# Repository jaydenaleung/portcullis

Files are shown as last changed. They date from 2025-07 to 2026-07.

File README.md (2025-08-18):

# Portcullis - the boltlock unlocker

A portcullis originally guarded a castle's entrance, known for its waffle-like iron gates coming down to cover the entrance of the castle's archway following the moat bridge.
-

Portcullis is an automated system that mechanically unlocks home security door reinforcement locks (HSDRLs), with access protected by a passcode using a keypad. HSDRLs act as boltlocks when mounted onto the doorframe next to the door being locked. See below for more information.

VIDEO DEMO: [https://youtu.be/WndzgAl9owI](url)






*The large block in the picture represents the wall that HSDRLs are mounted onto.*



*A medival portcullis. Credit: [https://www.dreamstime.com/stock-images-castle-portcullis-image7831724](url).*

# Figures

**Total Minimum Cost:** $43 USD

**Total Hours Spent:** 92 hrs

**Total Days Spent:** 16 days

*See JOURNAL.md and the BOM below for an in-depth explanation of these numbers.*

# How It Works

How do HSDRLs work?
-

HSDRLs lock a door by acting as a fixed stopper. In combination with this, their tough metal material allows it to be one of the strongest, safest, and most secure locks on the market. After turning them to their locked position, they will 'click' into place, effectively fixing itself against the door. Mechanically, this means that when the door pushes against it, its rigid position will hold the door back. See the picture below for how unlocking and locking an HSDRL works.



Portcullis
-

This specific mechanism works to solve this issue in three steps: one, using a linear actuator to push the HSDRL forward enough that it can be rotated. Two, rotate it to unlock or lock the door. Three, retract the linear actuator to lock the HSDRL in place. This is all controlled by an Arduino Uno R3 microcontroller, which connects to a continuous servo powering the linear actuator and a positional servo rotating the mechanism. Additionally, the locking/unlocking process is initiated by either entering the correct passcode on a keypad on the side of the door opposite the lock or by pressing a button (passcode not required) on the same side of the door as the lock.



Additional Features
-

- 16x2 LCD interface to display entered PIN from the keypad
- Privacy covers when entering PIN - numbers show up as '*' instead of the entered number
- Three different possible screens for the LCD display
- Aesthetic microcontroller housing with LED lights on button
- Linear guide rails and tension springs for the linear actuator

Wiring Diagram
-

This project does not utilize a PCB because of the sparse placement of the connected parts. See this wiring diagram instead:



And this schematic:



# The 'Why' Behind the Project

This project actually started a while ago when I wanted to ensure that no one would could come into my room without my permission, as I felt back then that it had become an issue. Using my engineering skills to solve real-world issues, I initially worked on developing my own boltlock before realizing that it would be much more efficient to just purchase a boltlock. Unfortunately, I would occasionally get locked out of my room, which was a significant issue. I again began to solve this issue by taking an engineering approach to it and working a system that could lock and unlock the boltlock for me when I was outside of my room. In addition to having a keypad, I envision pairing this mechanism with my phone so that it will be more easily accessible, especially if something happens to break or the wires to the keypad snap.

# Why This Is Worth Six Points

With the three-part unlocking/locking system mentioned earlier, this is a mechanically complex project that requires precise control of the motors in order to ensure reliability and stability. I spent many hours designing a system for this (over half of my hours spent were in CAD and research), learning a lot about linear guide rails, springs, and their standardizations, and how to effectively approach a real-life issue using engineering. Additionally, I spent a significant amount of time and effort designing logic for the keypad, LCD screens, and LED button as well as making them all work smoothly in tandem. My effort spent doing this project, seen in the thirty hours of work done in addition to prior work and excluding the process of physically building the device, qualifies this project for six points.

# Bill of Materials (BOM):

*Note: I am using Aliexpress for some and Amazon for others. Prices listed below are in USD and per part. e.g. 2x Nema 17 ($14) = $28 total. Also see the .csv file for the official BOM.*

| Quantity | Name | Price Per Part | Link | Notes |
|---|---|---|---|---|
| 2 | MGN7C linear guide rail + carriage | $12.78 | https://www.aliexpress.us/item/3256804722090559.html | 150mm length |
| 4 | M2 50pcs bolt | $1.27 | https://www.aliexpress.us/item/2255799955713291.html | 4mm, 6mm, 8mm, 10mm lengths |
| 1 | M2 50pcs nut | $1.52 | https://www.aliexpress.us/item/3256807407546447.html |  |
| 1 | M3 30pcs bolt | $1.43 | https://www.aliexpress.us/item/2255799955713291.html | 6mm length |
| 1 | M3 50pcs nut | $1.68 | https://www.aliexpress.us/item/3256807407546447.html |  |
| 1 | 10 pcs Tension spring w/ hook | $4.09 | http://www.aliexpress.us/item/3256805190632211.html | 50mm length, 0.3mm wire diameter, 5mm outer diameter |
| 2 | Pushbutton | $3.06 | https://www.aliexpress.us/item/3256807837994773.html | Red color (NOT with the power symbol), 3-6V, 19mm size, momentary type |
| 1 | 3m length wire cover | $5.39 | https://www.aliexpress.us/item/3256808858896776.html | A-White (A-type, white and red color) |
| 1 | Heat gun + Heat shrink tubes | $9.99 | https://www.aliexpress.us/item/3256807579039319.html | 1060 pcs, 110V US plug |
| 1 | Keypad | N/A | https://a.co/d/2Og2Gza | Already have this (no price). |
| 1 | LCD | $2.39 | https://www.aliexpress.us/item/3256806852105736.html | I2C LCD Green |
| 1 | Power bank + USB-B cable | N/A | Any works | Already have this (no price). |
| 1 | Positional SG90 Servo | N/A | https://a.co/d/dwwxeeT | Already have this (no price). |
| 1 | Continuous FS90R Servo | N/A | https://a.co/d/2raoKgm | Already have this (no price). |
| 1 | Jumper wires | N/A | https://a.co/d/hYEySLh | Already have this (no price). |
| 1 | 1kg spool of filament | N/A | Any works | Any color, any type. Already have this (no price). |
| 1 | Home security door reinforcement lock | N/A | https://a.co/d/iCTK5DP | Already have this (no price). |
| 1 | 330Ω resistor | N/A | N/A | Already have this (no price). |

| **Total minimum cost** | $43.41 |
| --- | ---- |
| **Total including shipping; sales tax (assumed ~6%); import and customs fees; etc.** | ~$75 |

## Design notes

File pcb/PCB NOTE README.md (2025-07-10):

There is no required PCB for this project because of the unique positioning of the electronic components. Since the components are on different sides of the doors and the parts are not positioned so that they can be mounted onto the PCB anyways, a PCB is not necessary. The PCB was included for your reference and also because I did not realize this until I had made the whole PCB.

The wiring diagram can, alternatively, be found here: [https://app.cirkitdesigner.com/project/c432579e-b21c-4e14-8d9b-45fb584a04a3](https://app.cirkitdesigner.com/project/c432579e-b21c-4e14-8d9b-45fb584a04a3).

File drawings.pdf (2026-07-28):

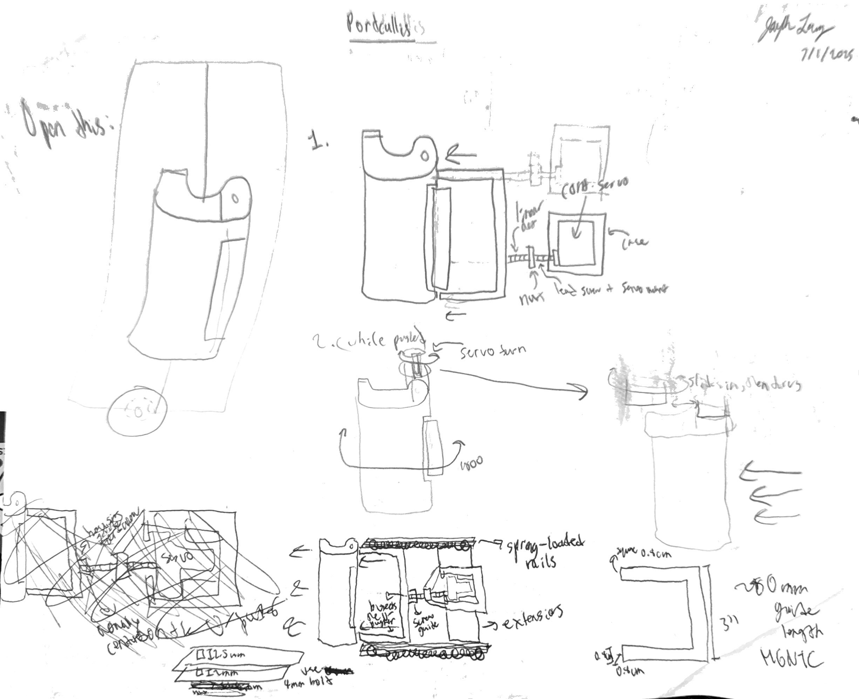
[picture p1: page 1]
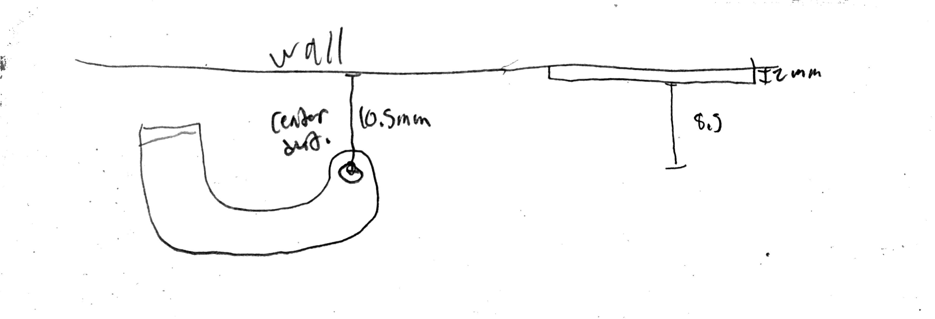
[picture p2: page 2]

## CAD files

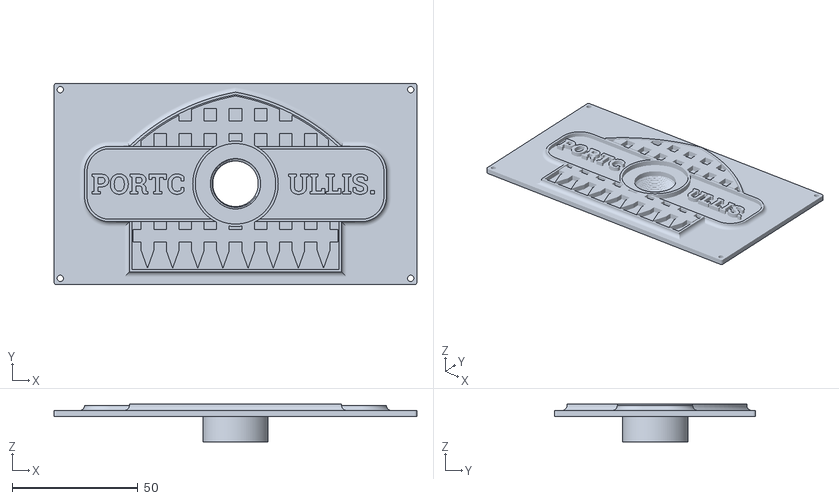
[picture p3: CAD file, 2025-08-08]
cad/parts to print/Arduino housing.stl
144.3 x 80.0 x 15.0

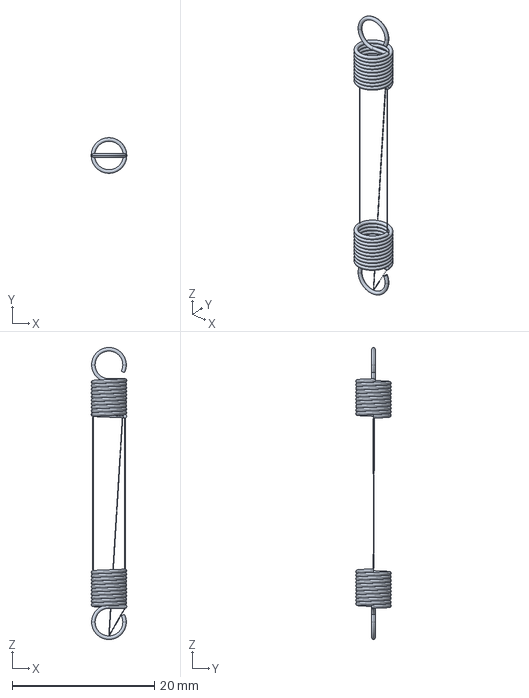
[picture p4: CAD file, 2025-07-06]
cad/reference parts/0.3mmWireD_5mmOutsideD_40mm_TorsionHookSpring/spring_t_050_050_0400_i_0.stp
5.00 x 5.00 x 41.0 mm

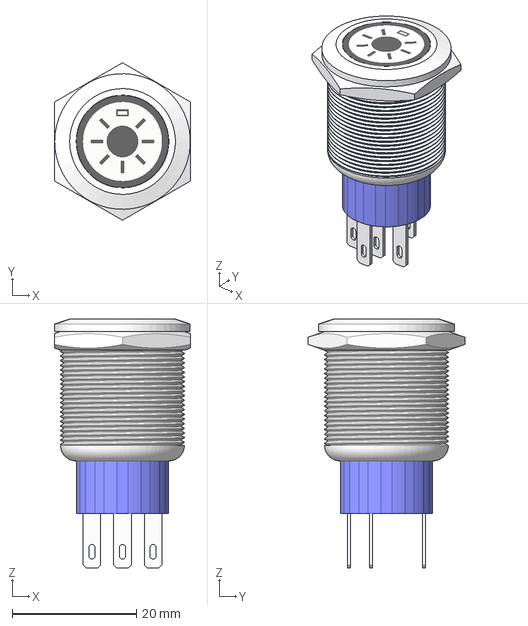
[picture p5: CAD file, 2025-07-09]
cad/reference parts/19mm_Momentary_OnOffButton/1_Push_Button v4.step
21.9 x 25.3 x 40.0 mm

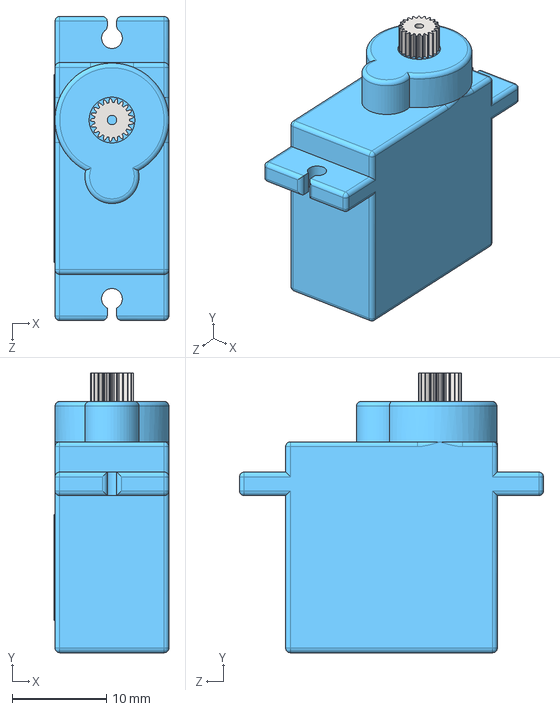
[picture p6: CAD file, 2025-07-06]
cad/reference parts/FITEC_FS90R_ContinuousServo/Fitec FS90R Micro Servo NoWires.STEP
12.2 x 29.7 x 32.3 mm

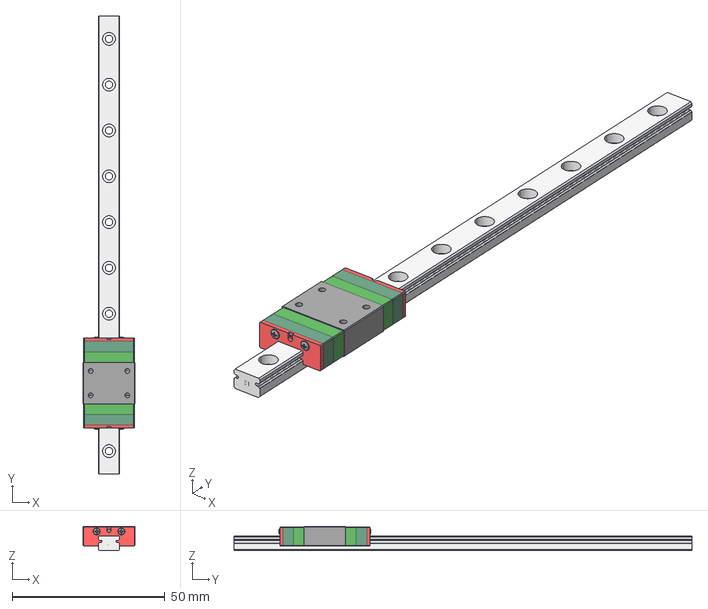
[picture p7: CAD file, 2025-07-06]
cad/reference parts/HIWIN_MGN7C_150mm_LinearGuideRail/MGN07C1R150ZFHM_EL_FILE_1.stp
17.0 x 150.0 x 8.00 mm

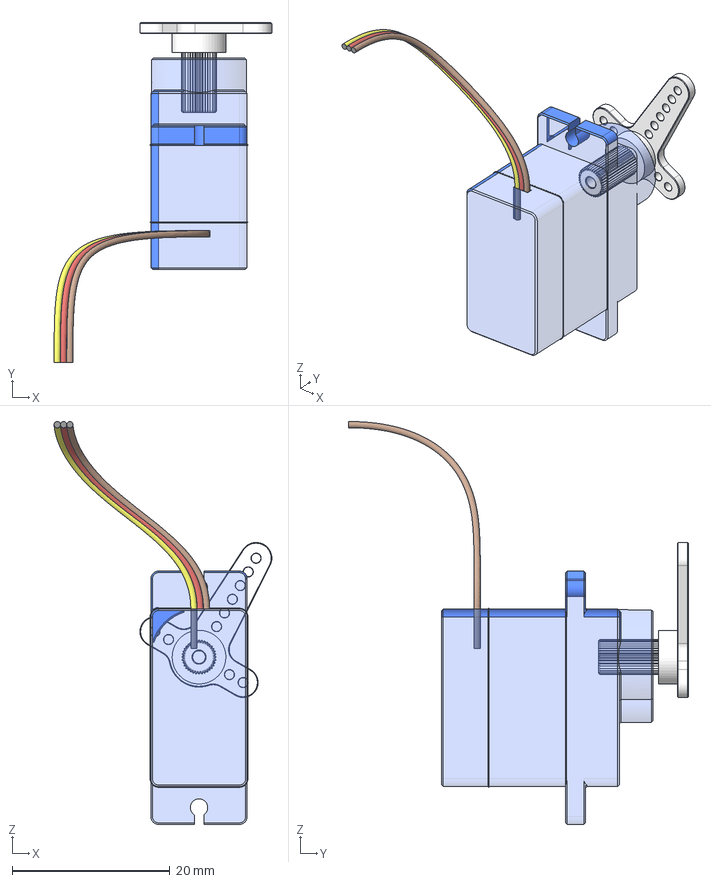
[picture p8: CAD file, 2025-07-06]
cad/reference parts/SG90_MicroServo/SG90 Servo.stp
27.6 x 43.0 x 51.0 mm
Servo_1
PernoServo
LevaServo

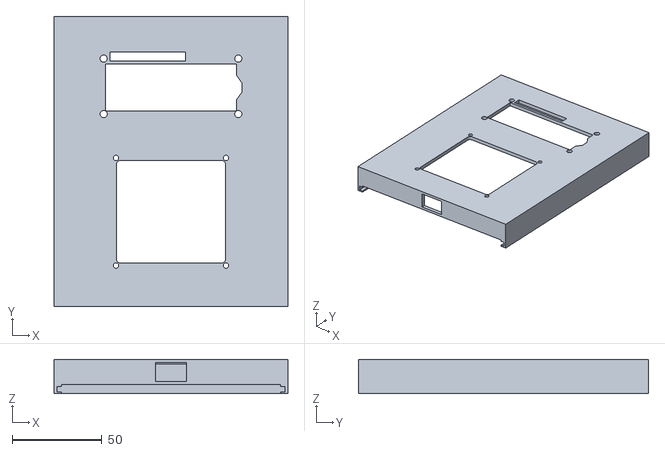
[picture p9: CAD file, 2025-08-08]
cad/parts to print/Frame.stl
130.2 x 161.5 x 19.1

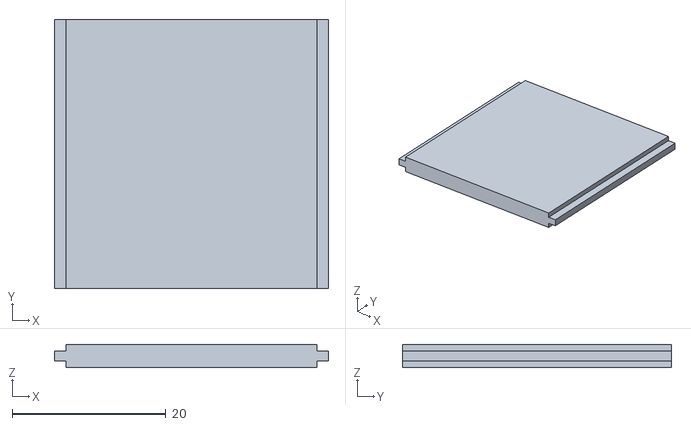
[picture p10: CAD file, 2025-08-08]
cad/parts to print/servo slider cover (2).stl
35.7 x 35.0 x 3.00

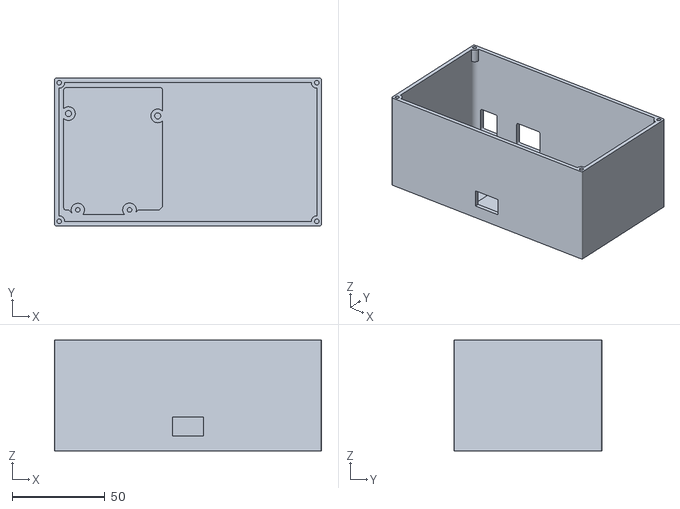
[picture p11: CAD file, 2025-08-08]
cad/parts to print/Arduino housing - bottom.stl
144.3 x 80.0 x 60.0

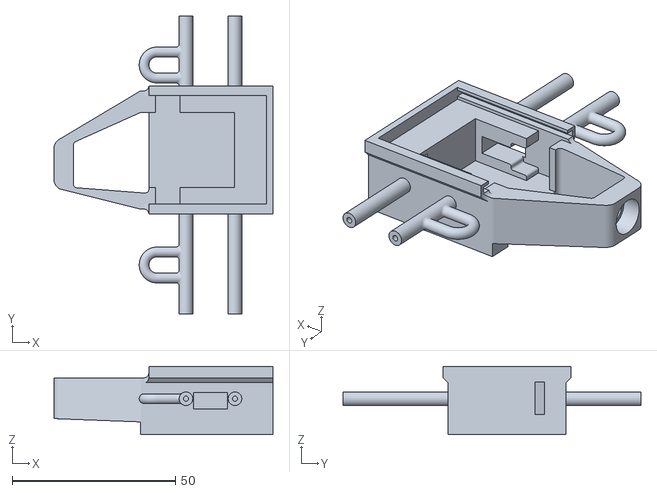
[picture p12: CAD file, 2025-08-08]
cad/parts to print/Servo Slider (1).stl
67.0 x 91.2 x 20.9

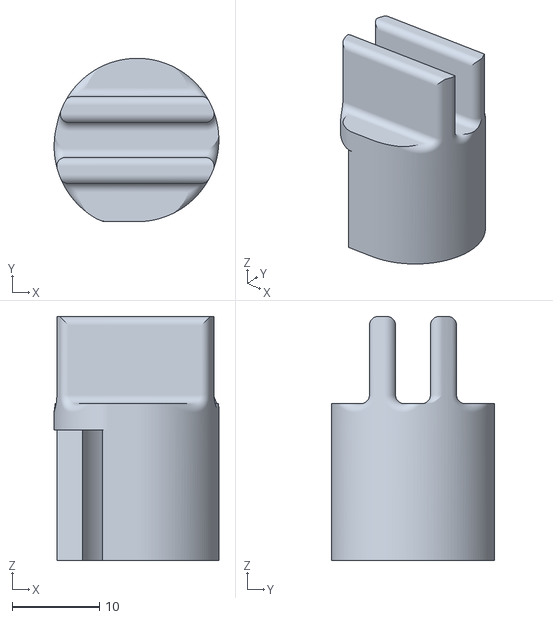
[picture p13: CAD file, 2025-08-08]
cad/parts to print/Lock Mount.stl
18.9 x 18.7 x 28.0

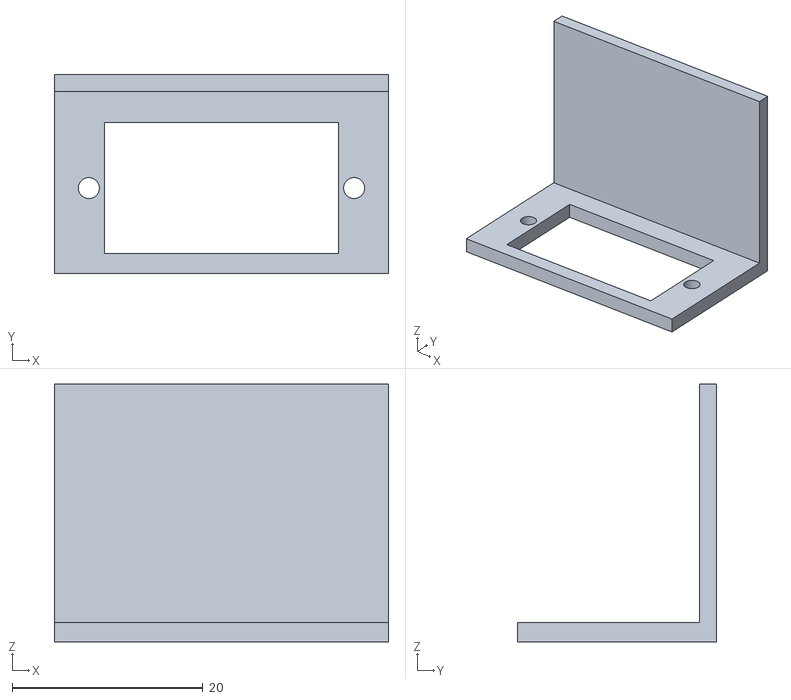
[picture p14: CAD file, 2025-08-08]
cad/parts to print/Servo housing.stl
35.0 x 20.8 x 27.0

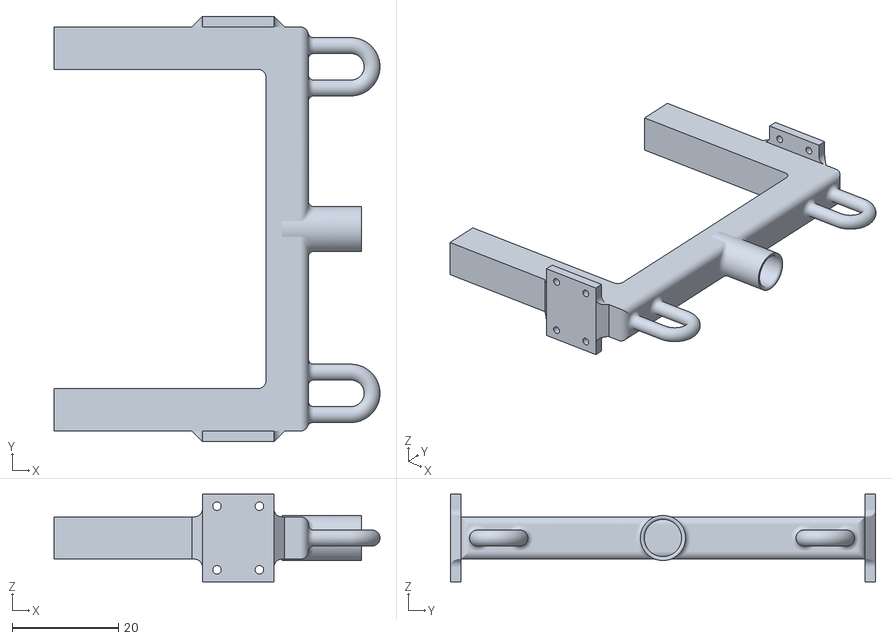
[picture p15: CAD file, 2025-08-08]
cad/parts to print/U-Pusher.stl
61.5 x 80.2 x 16.6

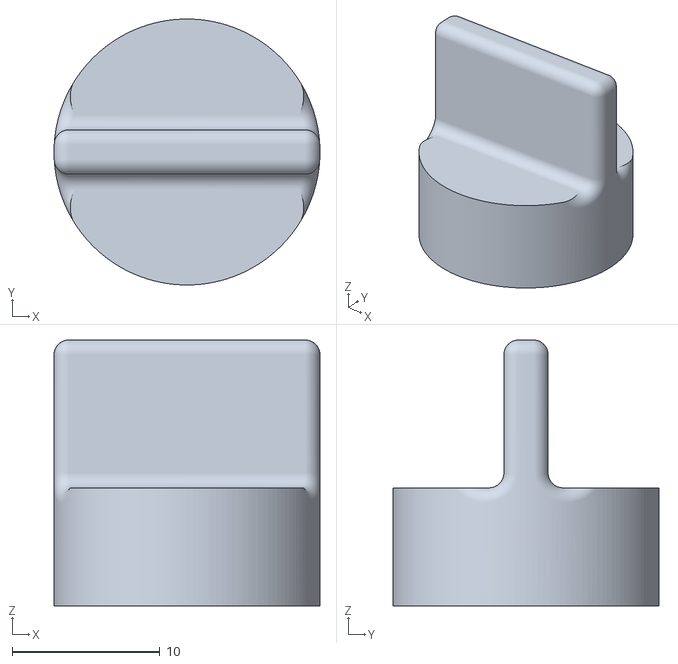
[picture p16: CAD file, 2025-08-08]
cad/parts to print/Servo Mount.stl
18.0 x 18.0 x 18.0

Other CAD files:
cad/parts to print/Frame Cover.stl
cad/parts to print/Extension cap.stl
cad/parts to print/Rail mount.stl
cad/parts to print/Washer (rails).stl
cad/parts to print/Nut (actuator).stl
cad/parts to print/Screw.stl

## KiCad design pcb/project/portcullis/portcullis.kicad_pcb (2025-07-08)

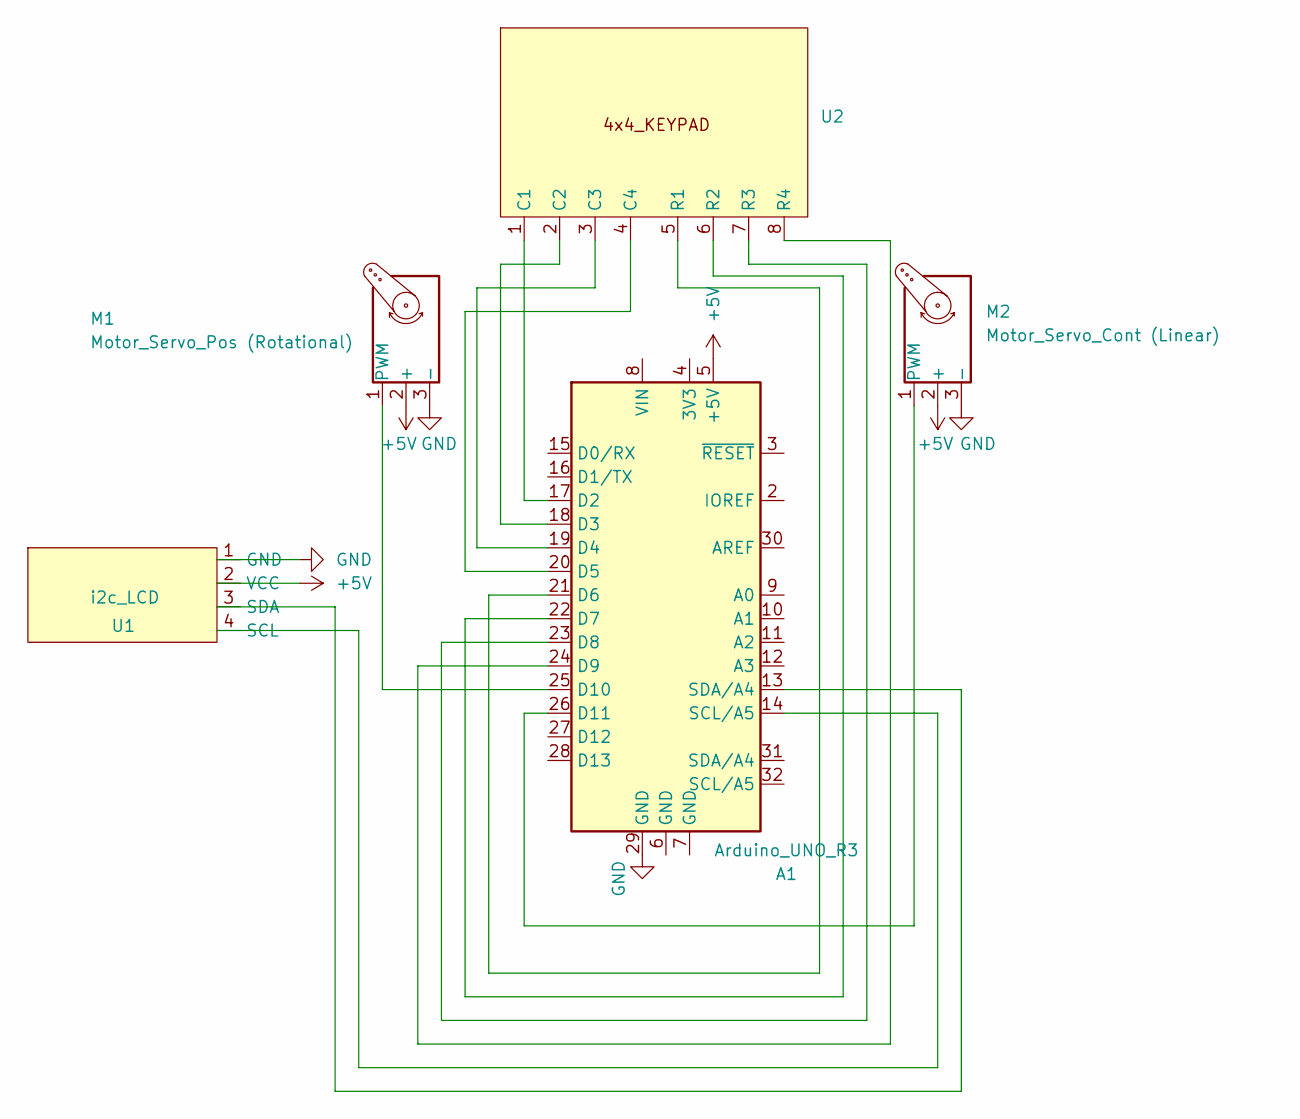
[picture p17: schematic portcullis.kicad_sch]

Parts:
A1: Arduino_UNO_R3; ARDUINO_ARDUINO_UNO_REV3
M1: Motor_Servo_Pos (Rotational); 3-Pin Servo
M2: Motor_Servo_Cont (Linear); 3-Pin Servo
U1: i2c_LCD
U2: 4x4 16 Button Keypad

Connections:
+5V: A1.5 (+5V), M1.2 (+), M2.2 (+), U1.2 (VCC)
GND: A1.29 (GND), M1.3 (-), M2.3 (-), U1.1 (GND)
unnamed: A1.17 (D2), U2.1 (C1)
unnamed: A1.18 (D3), U2.2 (C2)
unnamed: A1.19 (D4), U2.3 (C3)
unnamed: A1.20 (D5), U2.4 (C4)
unnamed: A1.21 (D6), U2.5 (R1)
unnamed: A1.22 (D7), U2.6 (R2)
unnamed: A1.23 (D8), U2.7 (R3)
unnamed: A1.24 (D9), U2.8 (R4)
unnamed: A1.25 (D10), M1.1 (PWM)
unnamed: A1.26 (D11), M2.1 (PWM)
unnamed: A1.14 (SCL/A5), U1.4 (SCL)
unnamed: A1.13 (SDA/A4), U1.3 (SDA)

Board: 2 copper layers, 5 parts (1 on the bottom side), 14 nets, no tracks yet.

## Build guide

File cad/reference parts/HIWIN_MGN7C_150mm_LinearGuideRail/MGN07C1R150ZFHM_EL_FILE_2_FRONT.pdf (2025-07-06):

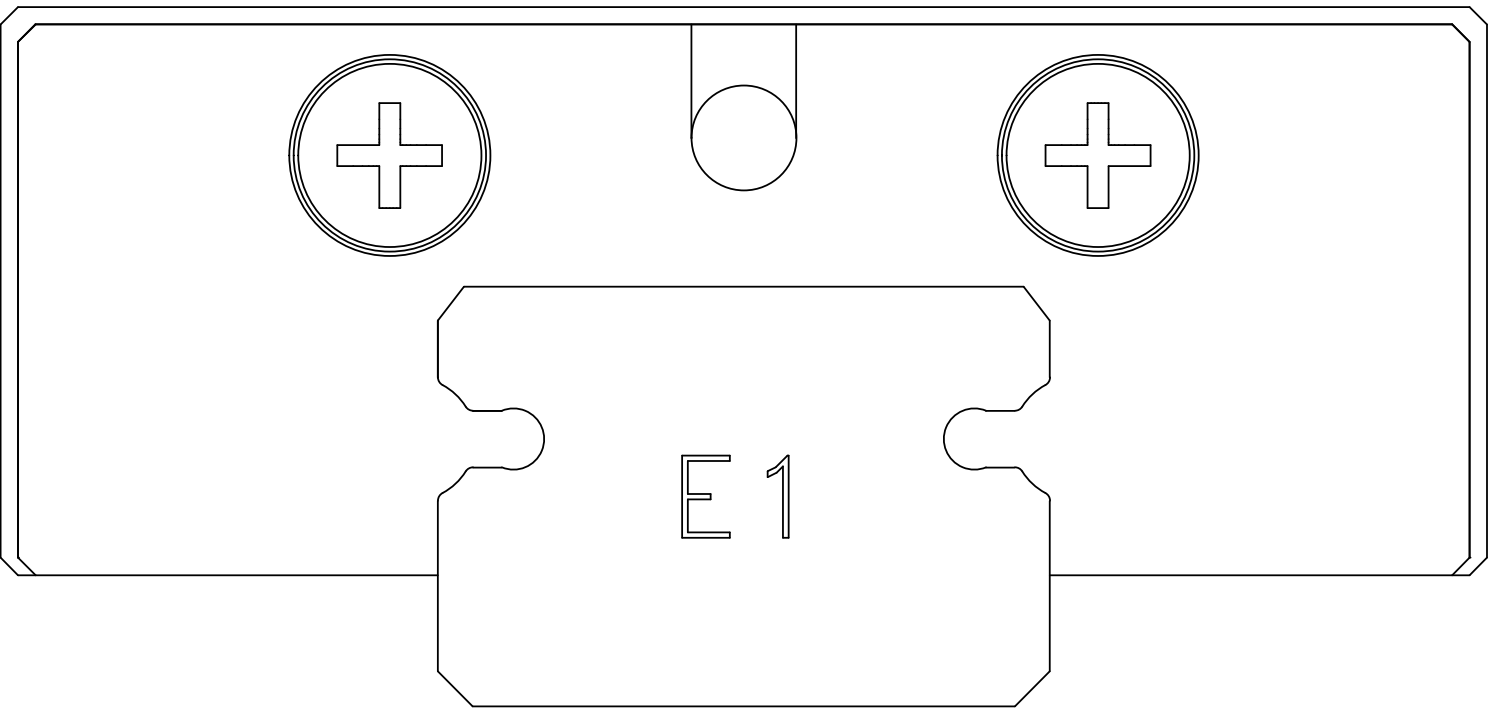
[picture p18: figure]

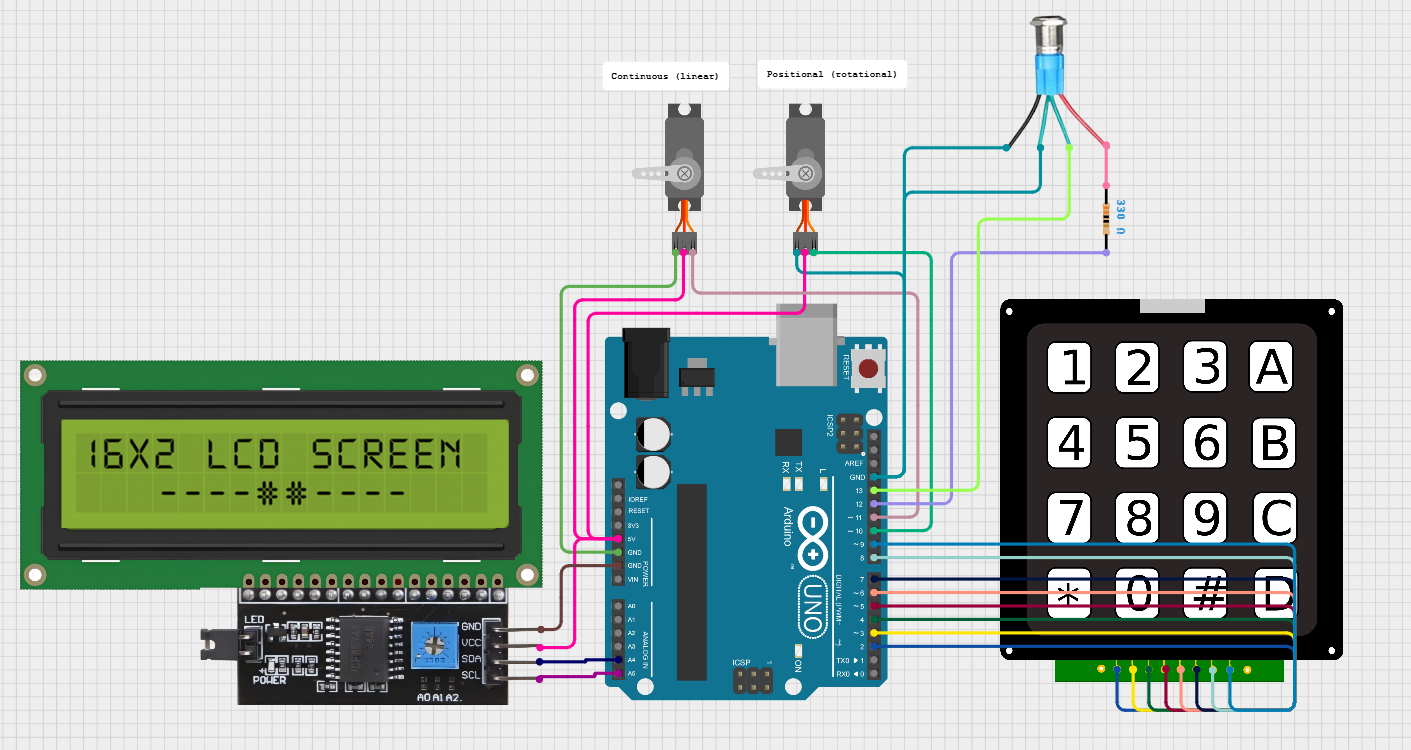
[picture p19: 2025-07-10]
pcb/wiring_diagram.png

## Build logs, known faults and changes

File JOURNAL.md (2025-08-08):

---
title: "Portcullis"
author: "Jayden Leung (Hack Club Slack: loliipoppi)"
description: "Automatic remote locking and unlocking system for home security door reinforcement locks moving along two conflicting axes."
created_at: "2025-07-01"
---

# Time Spent
- **Total hours excluding prior work: 92h**
- **Total days excluding prior work: 16 days**
- **Total days in prior work: ~3 days**
- **Time spent on CAD: 17h**
- **Time spent on PCB design: 4h**
- **Time spent on coding: 4h**
- **Time spent on physical assembly: 62h**
- **Time spent on sourcing parts, writing journal and readme, etc.: 5h**

# Prior Work

Originally, this project was called the "Keypad Autolock" when I worked on it before Highway. **However, I didn't have much of the project complete before Highway, so I decided that this could likely count for a project submission after consulting with others in the Slack.** Specifically, I had the case for the keypad, a model of the lock, a housing for the servo, and ideas for a linear actuator, among others, in place before Highway. **When I began this project for Highway, I still spent time doing research to figure out the most effective ways to navigate this mechanical engineering problem. I have still spent a significant amount of time in CAD, and I haven't done any prior PCB design work or firmware coding on this prior to Highway.**

The Keypad Autolock, now Portcullis (meaning the waffle-like iron gates that historically guarded castle doors following the drawbridge), is designed to open home security door reinforcement locks (HSDRLs) remotely using a keypad on the other side of the door. Alternatively (maybe in the future), I'm hoping that I can integrate remote connectivity to unlock and lock it from my phone.

**Total time spent (prior to Highway): 7h**

# July 1: Research

Prior to starting the project, I made sure to do my research. An HSDRL is a two-stage lock; it must first be pulled outwards and, after, rotated to be unlocked. However, the reason they were so secure - and difficult to unlock/lock with a mechanical design - is that these two axes were not the same. Consider an XYZ space with the Z axis pointing up/down and the XY plane lying flat. The HSDRL must first be pulled linearly along either the X/Y axis (a 'flat' axis) and then be rotated about the Z axis. This makes designing a remote locker/unlocker difficult as there needs to be two parts to the design. This also makes this project highly mechanical.

67695ae9-2831-491d-8d26-9c6d92e1358c __CR0,0,970,600_PT0_SX970_V1___

From my prior work, I already had an idea of how it might work, but I wanted to see if there were more effective ways to go about it. I finally settled on the method that made the most sense to me. This was to incorporate a linear actuator to push the lock outwards and then rotating the lock with a servo. Below is the finished CAD design (the research was done beforehand, the diagram is just there to visualize the system better), which illustrates the above explanation. I also realized halfway through designing it that I overcomplicated the design and that the entire linear actuator part could be simplified by having the screw go through the U-shaped part and locking the U-shaped part's ability to rotate. However, I didn't want my work to go to waste, so I decided to continue, which also benefitted me in allowing me to learn more about springs and linear guide rails.

Screenshot 2025-07-07 at 4 30 50 PM

**Total time spent: 1h**

# July 1-7: CAD

Then came the bulk of the project - CAD. Since this was a mechanically heavy project, I spent a good amount of time - about a week - on this part. Below is an in-depth explanation:

Keypad frame and housing:
- Housing box for the keypad, LCD, and PCB on the other side of the door
- Includes mounting holes on the housing and a hole for wires to exit the housing and travel under the door and to the Arduino microcontroller

Screenshot 2025-07-07 at 4 32 23 PM

Linear actuator: 
- Uses a continuous micro servo attached to a screw
- The housing for the servo allows it to slide linearly and includes a nut
- When the screw turns, it interacts with the nut and pulls itself and the servo forward
- The screw also touches (but is not connected to) the U-Pusher, a U-shaped part which pushes the lock linearly when the servo extends - this is the first step to unlocking the lock
- The U-Pusher and the servo housing are independent of each other and are not connected
- The U-Pusher and the servo housing are connected to a linear guide rail which allows the U-Pusher to slide closer and farther from the servo housing as the screw pulls forward/backward
- Springs are mounted to the U-Pusher and servo housing to keep the screw and U-Pusher together but not physically connected (implemented for when the screw retracts)

Screenshot 2025-07-07 at 4 33 00 PM

Rotational device:
- A cap is mounted onto the lock with two prongs extending upwards
- Another cap with one prong extending downward is mounted onto a positional servo and sits just to the side of the cap on the lock
- When the linear actuator pushes the lock, the prongs on both caps slide into place, next to each other
- The positional servo then turns the lock ~100° to fully unlock it
- (The linear actuator then retracts the screw to fix the lock into the unlocked position)

Screenshot 2025-07-07 at 4 36 20 PM

**Total time spent: 12h**

# July 7: PCB and Wiring

After I finished CADing, I moved onto PCB design. Now, after I finished designing my entire two-part PCB, I realized that it was much too impractical to even install one; in other words, I'd just wasted hours of my time. However, I wouldn't say it was entirely wasted, since I learned some valuable lessons:

One, think before you do! I tried this out when I was in the middle of designing the PCB late at night and realized what I was doing would overcomplicate the design and that there was a much simpler, faster, and more effective way to design my PCB. Two, I gained more experience and practice in PCB design, drawing footprints, etc. I found KiCAD's array feature which helped me to add multiple of the same type of through hole at once, saving me a lot of time and effort. Three, I needed a schematic anyway, and it helped me with my wiring diagram that I ended up making instead.

The PCB was not needed since different parts were on different sides of the door, and besides, even the servos that were on the same side were physically separated. It didn't make sense to have a PCB since I could not effectively mount all the parts. Instead, I would pass the wires under the door and plug them into the Arduino microcontroller, making sure to solder the 5V wires together and to secure the pins so that they wouldn't move.

Here's the schematic that I made:


Here's the PCB that I made (I saved it anyway):
Screenshot 2025-07-08 at 2 15 36 PM

Here's the wiring diagram that I'll be using:
unnamed

**Total time spent: 4h**

# July 8: Additional CAD

Usually, this would be the step where I would make changes to my CAD design to incorporate the PCB I just created. However, since a PCB wasn't needed for this project, I instead took this time to create a housing for my microcontroller, which also included a button I forgot to account for earlier. This button would also lock and unlock the door without needing a password (since it would be behind the door).





As you can see, I got a bit carried away in designing the case. I found a text FeatureScript in Onshape (a program that allowed me to add text into my CAD model), which would have been really helpful for my other hackpad project (I spent about an hour writing the text by hand using lines and curves). After that, I decided to make the case look like a real, medival portcullis, and I also wanted to include the button in the middle. It was nice to learn how to incorporate aesthetics in my CAD designs, though!

Additionally, I fixed up a few minor details with the servo housing and its cover. I also moved the hole in the keypad housing for the wires to pass out of to the bottom so I could attach my wire cover directly to the case.

**Total time spent: 5h**

# July 9-10: Firmware Coding

For the final piece of designing this project, I coded the firmware. It consisted of a few different parts: controlling the servos and the locking mechanism, the keypad logic to decide when to unlock or lock it, and updating the UI on the LCD. Coding the mechanical control of the servos wasn't too difficult except that I needed to get the angular speed of my continuous servo empirically, and I did not have the tools to do that at the moment. Instead, I went with 130 RPM, which is what the internet said was its max speed.

After that, I coded the keypad logic, which surprisingly was not as difficult as I imagined. Many conditionals, yes, but nothing too complicated. '*' meant clear the PIN, '#' meant enter, and everything else - including letters A-D and numbers 0-9 - was fair game for the PIN. However, the code began to get messy after I added in LCD text and LED light logic on top of that. But a few void-type functions for organization easily cleaned it up.

I thought I was finished, but it turned out that I had forgotten to include code for the LED light-up button on the inside of the door that allowed me to unlock and lock it without a passcode. It took me a few tries and some help from ChatGPT before I could get edge detection down, but I finally finished the program in 189 lines.



**Total time spent: 4h**

# July 27-August 1 - Putting It All Together, Mechanically

A huge package of all my materials came today (July 27), and since I previously had used my 3D printer to print all of the parts, I began putting it together. Here are some issues I encountered:

- The nut and screw I 3D printed didn't mate well, so I had to use a similar nut that I prototyped with before (that did work). I hot glued it onto the linear (continuous) servo housing. I also had to modify the housing a bit to fit the servo better.
- The hooks I made for the springs were way too thin, so I reprinted the housing with thicker hooks. This allowed me to put 4 springs on each of the two hooks, which provided excellent tension as the linear guide rails were a little rough.
- The linear guide rails were really greasy when they arrived, probably really coated in WD40 or another lubricant. I wiped them down with a tissue.
- The screws fit well with the 3D printed parts, **BUT HERE'S A BIG LESSON I LEARNED: 3D printed hole sizes can be smaller than it is in CAD!** Especially since I didn't have a really high quality Bambu or similar. I ended up having to scrape out some of the plastic in the hole to make it bigger and use a smaller screw.

Mechanically, the linear actuator worked well (except that the nut was falling off at the end), but the rotational actuator was a bit more of a pain. I reprinted it to be bigger, which helped to solve the problem.





# July 27-August 1 - Putting It All Together, Electrically

Ok, this was a **HUGE** pain. I literally spent two to three hours trying to figure out why my LCD module wasn't working, only to realize that the two LED jumper pins weren't connected. The biggest lesson I learned from this was probably about part sourcing and electronics in general.

**1. Never buy from Aliexpress, but always buy from Aliexpress.**

Wait, what? What I really mean is that the quality in Aliexpress is a lot lower than in Amazon or in-store, but they can have much cheaper prices. The best combination is to buy from an Aliexpress vendor that doesn't look sketchy (not the "Shop12312093712" vendor I purchased from), has at least 100-500+ of that item sold, has really good reviews, and has been operating for a 3-5 years minimum. 

*Better to have a slightly higher price than to have to buy a whole new one to replace it.* Low prices can be enticing - I can say that firsthandedly - but know they come at a cost. For example, I bought my keypad from a random seller on Amazon, and I didn't take the time to background-check their reputation before ordering it. I easily blew a trace on that keypad while soldering, rendering the entire thing useless.

**2. Expect to spend a lot of time on each electronic component. As a general rule of thumb, think of a reasonable time it would take and triple it. That's the time you need**

I spent a lot of time debugging, sometimes for the littlest things. *Don't overlook the smallest things! Double check your wiring!* Commonly used parts such as servos and buttons usually work, but remember to buy from a reputable seller. Sometimes the module is just broken or doesn't use the chip it says it uses to reduce manufacturing costs. It took me a long time to finally realize that I blew my keypad, and I couldn't use it (I couldn't get a replacement since I was leaving the next day, but I still mounted the broken keypad for the looks).

After that, I said I'd never become an electrical engineer (but computer engineer!). But now, I see that it might be kind of fun.


 |
 |
 V

 |
 |
 V
 
 |
 |
 V

 |
 |
 V
 

# July 27-August 1 - Putting It All Together, In The Code

I didn't initially use the code that I had previously designed since it was too fleshed out. Instead, I tested each part individually using example code. Surprisingly, at the end, my full code worked perfectly. It was kind of funny that the electrical part was the toughest, but the software somehow worked fine. Likely because I was using pretty simple and common parts for my build (servos, LCD modules, etc.).

# July 27-August 1 - Putting It All Together, Finally

After many, many tries, I finally finished it before I had to go off on a trip (where I couldn't access it) by pulling an epic all-nighter. Recording the setup, I turned on my power bank, waited for the setup to activate... the linear actuator pulled the servo forward, pushing the the boltlock... the tab on the servo slid into place with the boltlock... the rotational servo turned, and... it unlocked!!! I was so happy after spending basically the past 21 hours on it (which was just that day). For something that was supposed to be so simple, it took a long time. But I learned many lessons along the way, and that's what counts. Enjoy the video of it below!



Full Demo: [https://youtu.be/WndzgAl9owI](url)

P.S. It was meant to keep others out of my room, but the fragile setup seems to keep me more out of my room instead... maybe I'll improve it later!

**Total time spent (for the entire physical assembly): 62h**

*Note: This took a long time, but the time to build electronics projects should decrease as I gain more experience. This was my first ever fully built-and-finished project!*

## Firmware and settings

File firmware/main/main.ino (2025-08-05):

// include libraries
#include <Servo.h>
#include <Keypad.h>
#include <LiquidCrystal_I2C.h>

// init servos
Servo linear; // continuous linear servo
Servo rot; // positional rotational servo

// init LCD
LiquidCrystal_I2C lcd(0x27, 16, 2);

// setup keypad
const byte ROWS = 4; // Four rows
const byte COLS = 4; // Four columns

char keys[ROWS][COLS] = {
{'1', '2', '3', 'A'},
{'4', '5', '6', 'B'},
{'7', '8', '9', 'C'},
{'*', '0', '#', 'D'}
};

byte rowPins[ROWS] = {6, 7, 8, 9}; // Connect to row pins in format {R1, R2, R3, R4}
byte colPins[COLS] = {2, 3, 4, 5}; // Connect to column pins in format {C1, C2, C3, C4}

Keypad keypad = Keypad(makeKeymap(keys), rowPins, colPins, ROWS, COLS);

String PIN = "0000"; // SET YOUR PIN HERE
String attemptPIN = "";
bool lockedState = true;

// define pins
int linearPin = 11;
int rotPin = 10;

int ledPin = 12;
int buttonPin = 13; // button on the inside of the door

// variables, consts, and other states
bool lastButton = HIGH; // INPUT_PULLUP is default HIGH
bool actionDone = false; 

double msPerPush = 4000.0; // DETERMINED EMPIRICALLY

void setup() {
  Serial.begin(9600);
  
  lcd.init();
  lcd.backlight();
  lcd.setCursor(0,0);
  
  linear.attach(linearPin);
  linear.write(90);
  rot.attach(rotPin);
  rot.write(180); // starting position to mount onto the lock

  pinMode(ledPin, OUTPUT);
  pinMode(buttonPin, INPUT_PULLUP);

  enterPIN(); // set LCD screen to home
}

void loop() {
  char key = keypad.getKey(); // detect key press and save the key
  if (key) { // keypad logic
    if (key == '*') { // clear attempt
      attemptPIN = "";
      updatePIN();
    } else if (key == '#') { // enter
      if (attemptPIN == PIN) {
        accessGranted(); // update LCD
        updateLED();
        (lockedState == true) ? unlock() : lock();
        enterPIN(); // return LCD screen to home
      } else {
        accessDenied();
      }
      attemptPIN = "";
      updatePIN();
    } else { // add key pressed to the attempt
      if (attemptPIN.length() <= 4) { // only if the attempt isn't 4 digits yet
        String num = String(key);
        attemptPIN += num;
        updatePIN();
      }
    }
  }
  
  bool currentButton = digitalRead(buttonPin);

  if (currentButton == LOW && lastButton == HIGH && !actionDone) { // runs  once when pressed
    updateLED();
    (lockedState == true) ? unlock() : lock(); // do the action
    actionDone = true; // ensure that this code runs only once when pressed
  }
  if (currentButton == HIGH) {
    actionDone = false; // reset actionDone upon release of button
  }
  
  lastButton = currentButton; // update lastButton  
}

// LED
void updateLED() {
  if (lockedState == true) { // LED logic
    digitalWrite(ledPin, HIGH);
  } else {
    digitalWrite(ledPin, LOW);
  }
}


// LCD
void enterPIN() {
  lcd.clear();
  lcd.setCursor(0,0);
  lcd.print("Welcome, JAYDEN");
  lcd.setCursor(0,1);
  lcd.print("____");
}

void updatePIN() {
  lcd.setCursor(0,1);

  if (attemptPIN.length() > 0) { // hide the PIN that is typed in with stars
    String stars = "";
    for (int i = 0; i < attemptPIN.length(); i++) {
      stars += "*";
    }
    lcd.print(stars);
  }

  if (attemptPIN.length() < 4) {
    lcd.setCursor(attemptPIN.length(),1); // position the cursor after the last star
    String underscores = "";
    for (int j = 0; j < (4-attemptPIN.length()); j++) {
      underscores += "_"; // write underscores for any place where there is not a star within the 4-character PIN range
    }
    lcd.print(underscores);
  }
}

void accessGranted() {
  lcd.clear();
  lcd.setCursor(0,0);
  lcd.print("ACCESS GRANTED");
  lcd.setCursor(0,1);
  if (lockedState == true) {
    lcd.print("Unlocking...");
  } else {
    lcd.print("Locking...");
  }
}

void accessDenied() {
  lcd.clear();
  lcd.setCursor(0,0);
  lcd.print("ACCESS DENIED");
  lcd.setCursor(0,1);
  lcd.print("Incorrect PIN.");
  delay(3000); // wait 3s
  enterPIN(); // return LCD to home screen
}


// Servo control
void push() { // continuous linear servo
  linear.write(180); // push outwards
  delay(int(msPerPush));
  linear.write(90); // then stop pushing
}

void pull() { // continuous linear servo
  linear.write(0); // pull inwards
  delay(int(msPerPush));
  linear.write(90);
}

void turnUnlock() {
  rot.write(0);
  delay(500); // wait for it to rotate

void turnLock() {
  rot.write(180); // 90 deg is the angle to turn to the locked position, but 180 deg is used to push more firmly against the door
  delay(500); // wait for it to rotate
}

void unlock() {
  push();
  turnUnlock();
  pull();
}

void lock() {
  push();
  turnLock();
  pull();
  rot.write(90); // return it to the desired position after allowing it to push firmly against the door
}

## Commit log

2025-07-08 pcb finish pt 1
    [portcullis.kicad_pcb, portcullis.kicad_sch]
2025-07-11 cad and readme
    [Extension cap.stl, Frame Cover.stl, Frame.stl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]
2025-07-16 added gcodes
    [Arduino housing - bottom.stl, Arduino housing - top.stl, Arduino housing.stl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]
2025-08-08 Update cad files and assembly for jounal
    [Arduino housing - bottom.stl, Arduino housing - top.stl, Arduino housing.stl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]
